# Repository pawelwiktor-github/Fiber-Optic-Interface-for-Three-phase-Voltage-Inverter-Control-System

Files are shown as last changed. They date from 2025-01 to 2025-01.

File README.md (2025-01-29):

# Fiber-Optic-Interface-for-Three-phase-Voltage-Inverter-Control-System

## Table of Contests

1. [Introduction](#introduction)
2. [Abstract of Thesis](#abstract-of-thesis)
3. [Usage Instructions](#usage-instructions)

## Introduction
This repository refers to the creation and implementation of the Fiber Optic Interface for Three phase Voltage Inverter Control System for PMSM motors. Every schematics, auxiliary files and performed steps are described in [engineering thesis](/thesis/Projekt%20i%20wykonanie%20interfejsu%20światłowodowego%20dla%20układu%20sterowania%20trójfazowego%20falownika%20napięcia%20dedykowanego%20dla%20silników%20PMSM.pdf). Main task was executed in Altium Designer Professional software ([engineering project](/main/Fibre-Optic-Interface.PrjPcb)). Additional documentations of used components and mechanical diagrams are stored in [doc](/doc/) folder.

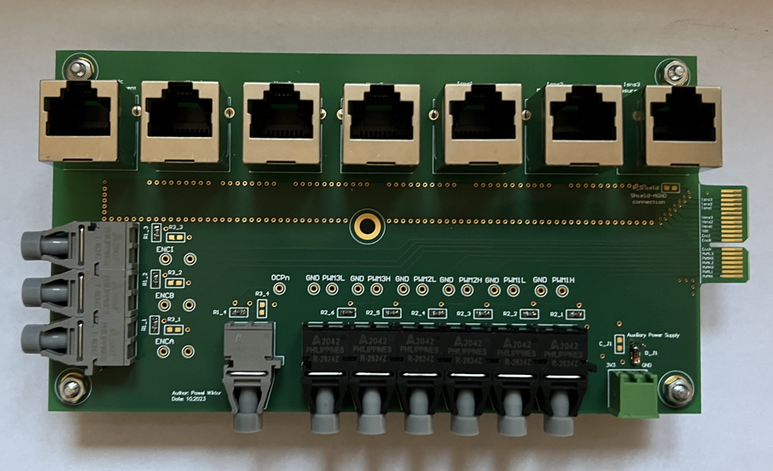
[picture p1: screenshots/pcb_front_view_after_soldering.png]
pcb_front_view
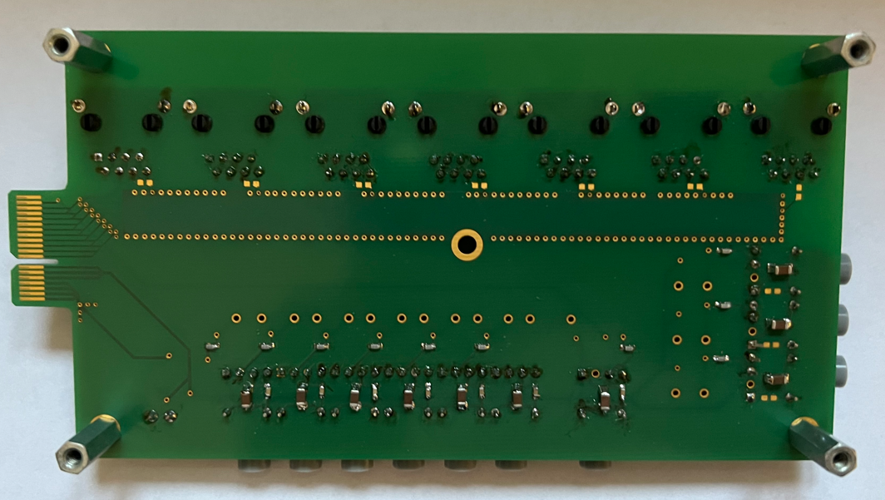
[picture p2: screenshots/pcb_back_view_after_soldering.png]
pcb_back_view
  

## Abstract of Thesis
The diploma project entitled as “Design and Implementation of Fiber Optic Interface for Three
phase Voltage Inverter Control System for PMSM Motors” describes steps related to the construction 
of a communication interface, which enables connection of three-phase voltage inverter module 
EPC9167 dedicated to drive systems with permanent magnet synchronous motors, made in “TTL” 
standard with a rapid prototyping controller B-BOX made in fiber-optic transmission standard.  
Engineering thesis includes a test bench description of the PMSM motor test system comprising 
of the above-mentioned components with their specifications, presents design requirements and 
created technical documentation of the interface and documents the assembly and testing processes.  
The project was finished with conclusions of communication interfaces designing process, an 
opinion on the encountered problems and opportunities for development. 

## Usage Instructions
**Prerequisites**:

***Software***:
   - Altium Designer Proffesional 24.8.2+

***Hardware***:
   - Fibre Optic Interface
   - BBox RCP Controller
   - PMSM Motor
   - EPC9167 (Three phase Voltage Inverter)

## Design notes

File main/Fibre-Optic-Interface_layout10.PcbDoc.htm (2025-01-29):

Reporting Options

# File in Newer Format

Date | : | 22.11.2023
Time | : | 11:46:45
Filename | : | C:\Users\Adam\Mój dysk (penczek@agh.edu.pl)\Dydaktyka\2023-24\Prace dyplomowe\Fibre_OPTIC\Altium\Fibre-Optic-Interface_rev9\Fibre-Optic-Interface\Fibre-Optic-Interface_layout10.PcbDoc

Version | Warning
Release 23.6 | CAUTION - The PCB document contains Footprint parameters. These will be lost when opening the document in a version of Altium Designer that does not support this functionality.

This file was generated by a later version of the software

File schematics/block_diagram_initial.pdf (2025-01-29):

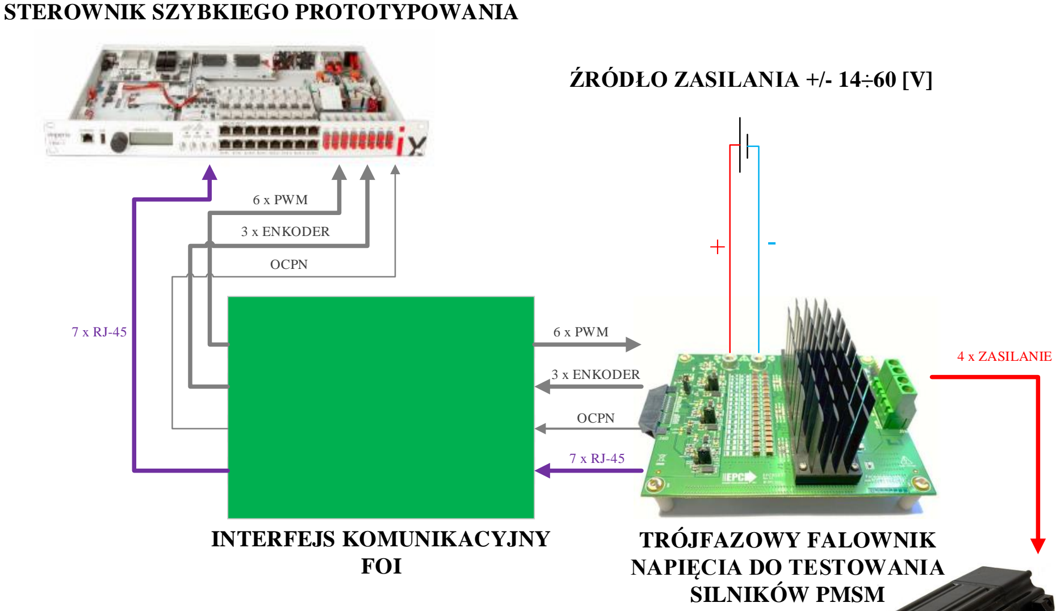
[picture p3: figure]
INTERFEJS KOMUNIKACYJNY FOI; STEROWNIK SZYBKIEGO PROTOTYPOWANIA; ŹRÓDŁO ZASILANIA +/- 14÷60 [V]; OCPN; 3 x ENKODER; 6 x PWM; TRÓJFAZOWY FALOWNIK; NAPIĘCIA DO TESTOWANIA SILNIKÓW PMSM; 4 x ZASILANIE
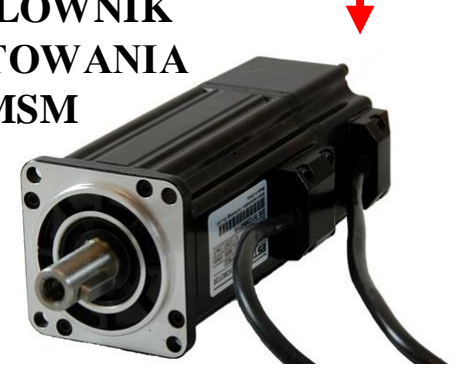
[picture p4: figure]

SILNIK PMSM

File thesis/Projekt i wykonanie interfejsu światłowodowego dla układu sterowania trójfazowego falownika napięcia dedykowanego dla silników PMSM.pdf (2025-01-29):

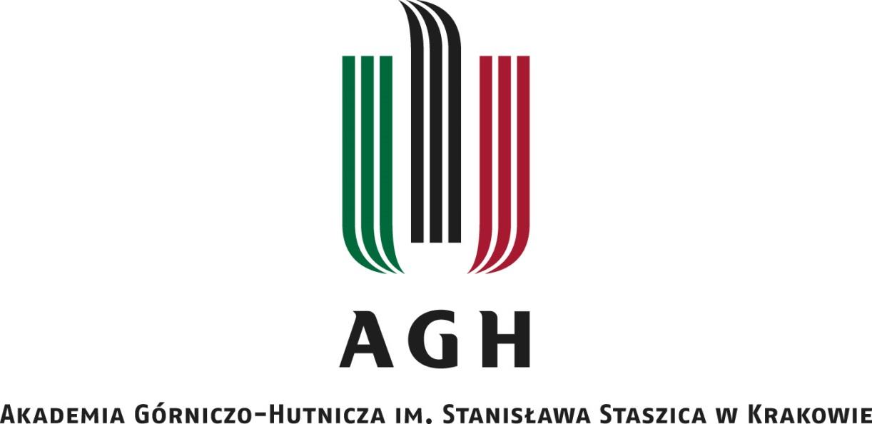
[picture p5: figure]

WYDZIAŁ ELEKTROTECHNIKI, AUTOMATYKI, INFORMATYKI I INŻYNIERII BIOMEDYCZNEJ

## Projekt dyplomowy

## Projekt i wykonanie interfejsu światłowodowego dla układu sterowania trójfazowego falownika napięcia dedykowanego dla silników PMSM Design and Implementation of Fiber Optic Interface for Three-phase Voltage Inverter Control System for PMSM Motors

Autor: | Paweł Wojciech Wiktor
Kierunek studiów: | Elektrotechnika
Opiekun pracy: | dr hab. inż. Adam Penczek

Kraków, 2024

Spis treści

Rozdział 3 – Projekt obwodu interfejsu światłowodowego dla układu sterowania trójfazowego

## Streszczenie

W projekcie dyplomowym pod tytułem „Projekt i wykonanie interfejsu światłowodowego dla układu sterowania trójfazowego falownika napięcia dedykowanego dla silników PMSM” opisano czynności związane ze skonstruowaniem interfejsu komunikacyjnego, który umożliwia połączenie wyprowadzeń obiektu w postaci modułu trójfazowego falownika napięcia EPC9167 dedykowanego
dla | układów | napędowych | z | silnikami | o | magnesach | trwałych, | wykonanych
w standardzie „TTL” wraz z wyprowadzeniami systemu szybkiego prototypowania dla układów sterowania B-BOX wykonanymi w standardzie transmisji światłowodowej.
W pracy inżynierskiej zawarto opis stanowiska badawczego systemu do testowania silników PMSM składającego się z wyżej wymienionych elementów wraz z ich specyfikacjami, przedstawiono założenia projektowe i stworzoną dokumentację techniczną interfejsu oraz udokumentowano procesy montażu i testowania.
Projekt zakończono podsumowaniem zawierającym wnioski dotyczące projektowania interfejsów komunikacyjnych, opinię na temat napotkanych problemów oraz możliwości rozwoju.

________________________________________________________________________________

## Abstract

The diploma project entitled as “Design and Implementation of Fiber Optic Interface for Three-phase Voltage Inverter Control System for PMSM Motors” describes steps related to the construction of a communication interface, which enables connection of three-phase voltage inverter module EPC9167 dedicated to drive systems with permanent magnet synchronous motors, made in “TTL” standard with a rapid prototyping controller B-BOX made in fiber-optic transmission standard. Engineering thesis includes a test bench description of the PMSM motor test system comprising of the above-mentioned components with their specifications, presents design requirements and created technical documentation of the interface and documents the assembly and testing processes. The project was finished with conclusions of communication interfaces designing process, an opinion on the encountered problems and opportunities for development.

## Rozdział 1. Wstęp

### 1.1. Wprowadzenie

Rozwój technologii w dziedzinie elektroniki mocy oraz sterowania silnikami stawia przed projektantami wyzwania związane z minimalizacją rozmiaru, zwiększaniem funkcjonalności i sprawności oraz ze zmniejszaniem poboru energii. Jednym z rozwiązań jest implementacja zaawansowanych układów elektronicznych zmieniających napięcie stałe na napięcie zmienne w procesie sterowania silnikami PMSM.
Silniki PMSM zyskują coraz większą popularność jako urządzenia wykorzystane na przykład w sprzętach AGD domowego użytku ze względu na swoje właściwości dynamiczne, wysoką sprawność oraz niskie zużycie energii.
Przed przystąpieniem do masowej produkcji konkretnego systemu należy określić zapotrzebowanie ilości sygnałów sterujących i parametrów sterowania. W fazie testowania można do tego wykorzystać sterowniki szybkiego prototypowania, które posiadają „przewymiarowaną” oraz zróżnicowaną ilość wyprowadzeń zarówno cyfrowych jak i analogowych.
Wśród sterowników szybkiego prototypowania, korzystnym wyborem są modele oparte na technologii w standardzie transmisji światłowodowej. Zaletami takiego rozwiązania jest możliwość propagacji danych na duże odległości, eliminacja problemów związanych z utratą sygnału, niski czas propagacji czy brak utraty jakości sygnału.
Aby była możliwość implementacji systemu szybkiego prototypowania, należy dopasować standard wyprowadzeń tego systemu do obiektu sterowanego. Zapewnienie komunikacji pomiędzy urządzeniami, które mają skonfigurowane wejścia i wyjścia w różnych standardach można uzyskać poprzez stworzenie interfejsu komunikacyjnego.
W przypadku standardu transmisji światłowodowej, wykorzystuje się interfejsy oparte na konwerterach, które oprócz translacji światłowodowo-elektrycznej zapewniają izolację galwaniczną – jeden z wymogów układów prototypowania.

### 1.2. Cel oraz zakres projektu dyplomowego

Celem projektu dyplomowego jest stworzenie obwodu drukowanego, umożliwiającego połączenie obiektu w postaci trójfazowego falownika napięcia EPC9167 dedykowanego do obsługi układów napędowych z silnikami PMSM z systemem szybkiego prototypowania układów sterowania B-BOX firmy „imperix”.
Podstawową funkcją jaką ma spełniać projektowany układ jest konwersja sygnałów logicznych w standardzie transmisji światłowodowej obsługiwanych przez sterownik B-BOX na cyfrowe sygnały elektryczne w standardzie „TTL” obsługiwane przez moduł falownika. Dodatkową funkcją jest rozprowadzenie sygnałów pomiarowych w standardzie analogowym wykorzystując złącza RJ-45 tak, aby można je było w łatwy sposób podłączyć do sterownika B-BOX.
Projekt dyplomowy obejmuje swym zakresem podział na trzy etapy.

W pierwszej części należy wykonać opis systemu, dla którego projektowany jest interfejs, czyli układu do szybkiego prototypowania systemów sterowania dla zespołów napędowych takich jak silniki PMSM, który zawiera obiekt sterowany w postaci silnika i modułu trójfazowego falownika napięcia oraz obiekt wymuszający w postaci sterownika RCP.
W etapie drugim nazwanym jako etap projektowy należy przedstawić założenia projektowe oraz zaprezentować stworzoną dokumentację techniczną interfejsu światłowodowego. Do stworzenia dokumentacji przewidziano wykorzystanie profesjonalnego oprogramowania „Altium Designer Professional (23.9.2)”.
Po uzyskaniu egzemplarza płytki, w ostatnim etapie należy zawrzeć opis procesu montażu oraz procesów testowania układu.

## Rozdział 2 – Opis systemu sterowania dla silników PMSM

Celem projektu było skonstruowanie urządzenia umożliwiającego połączenie sterownika B-BOX firmy „imperix”, którego wyprowadzenia wykonano w standardzie transmisji światłowodowej oraz modułu trójfazowego falownika EPC9167 firmy „EPC” o wyprowadzeniach wykonanych w standardzie „TTL”. Obiekt sterowany w postaci silnika z przekształtnikiem DC/AC, obiekt wymuszający w postaci systemu szybkiego prototypowania układów sterowania oraz interfejs komunikacyjny tworzą stanowisko do testowania układów napędowych pokroju silników PMSM, którego schemat blokowy zaprezentowano na rysunku 1.

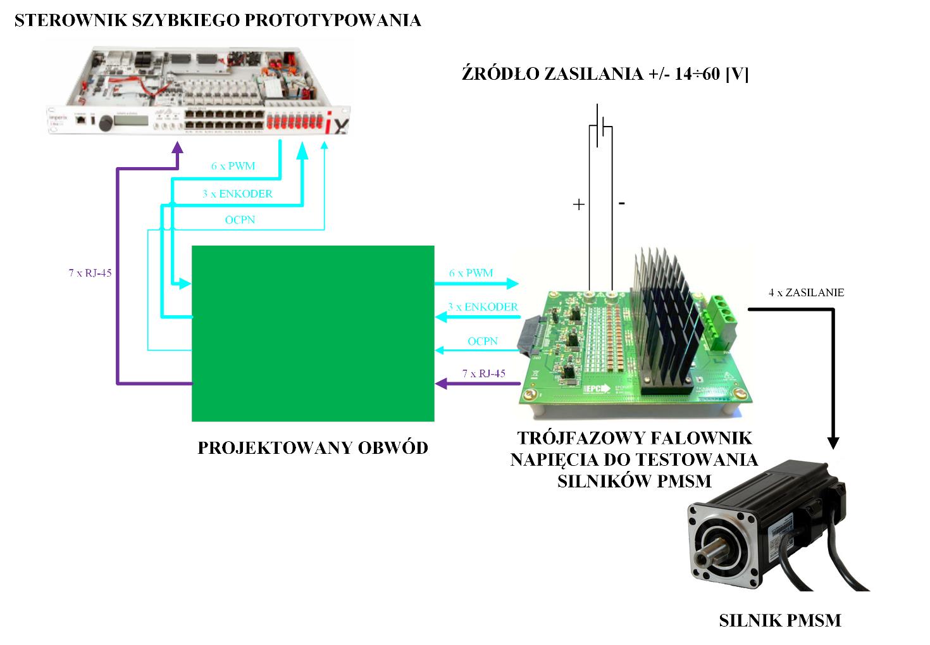
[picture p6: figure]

Rysunek 1. Schemat blokowy systemu sterowania

### 2.1. Sterownik B-BOX RCP

Sterownik B-BOX firmy „imperix” to system szybkiego prototypowania układów sterowania. Do zalet tego modelu zalicza się możliwość testowania układów obciążenia z racji posiadania większej ilości wejść i wyjść niż wymaga tego aplikacja oraz możliwość programowania blokowego, które jest proste oraz wygodne w obsłudze dla użytkownika. Na rysunku 2 przedstawiono zdjęcie sterownika B-BOX RCP.

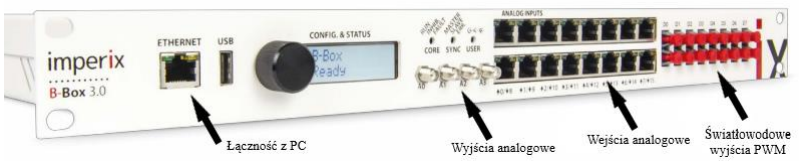
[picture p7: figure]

Rysunek 2. Zdjęcie sterownika imperix B-BOX RCP [1]

Model wyróżnia się zaawansowanymi możliwościami modulacji szerokości impulsu oraz licznymi wejściami/wyjściami analogowymi i cyfrowymi. Posiada również możliwość łączności z komputerem, a więc umożliwia współpracę ze zintegrowanym środowiskiem projektowania algorytmów blokowych pokroju oprogramowania „Matlab” z rozszerzeniem „Simulink”. Sterownik posiada wyprowadzenia wejść analogowych w standardzie RJ-45. Koncepcję przyłączenia sygnałów do pinów złącza przewidywaną przez producenta przedstawiono na rysunku 3.

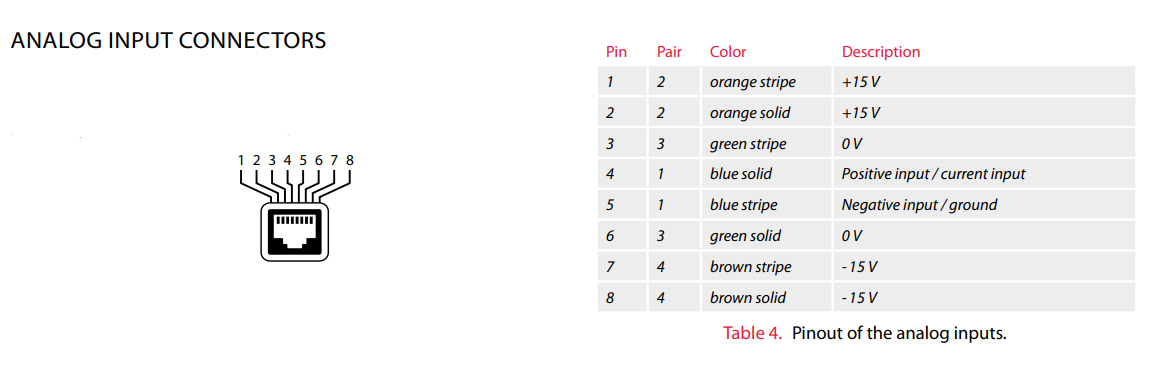
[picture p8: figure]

Rysunek 3. Koncepcja przyłączenia sygnałów do pinów złącza RJ-45 [1]

W tabeli 1 wyszczególniono główne specyfikacje sterownika, które są wykorzystywane przez aplikację FOI.

Tabela 1. Specyfikacje sterownika "B-BOX RCP" [1]

Komponent | Specyfikacja
Chip systemowy | Xilinx Zynq XC7030-3FBG676E, Klasa prędkości -3
System przetwarzania | ARM Cortex A9 1 [GHz] (2szt.), 1 [GB] DDR3
Programowalny układ logiczny (FPGA) | Kintex7 125K, Artix 7 35T (pomocniczy)
Przechowywanie | Pamięć flash 16 [MB] (2szt.), micro SD + eMMC 8 [GB]
Wyjścia PWM | Różne modulatory, rozdzielczość 4 [ns]
Optyczne 50 [Mb/s] (16szt.) Elektryczne [3.3 V] (32szt.)
Wejścia analogowe | 16 bitów / 500 ksps jednocześnie (16szt.) + w pełni konfigurowalny front-end
Szybkie wejścia/wyjścia użytkownika | FPGA bezpośrednie [3.3 V] (36szt.)
Wejścia/wyjścia błędów | Cyfrowe [3.3 V] (16szt.), blokada optyczna, blokada elektryczna [5 V]

Szczegółowa specyfikacja oraz schematy poszczególnych komponentów znajdują się w dokumentacji technicznej sterownika umieszczonej jako załącznik 1 niniejszej pracy.

### 2.2. Moduł trójfazowego falownika napięcia

EPC9167 to zestaw uruchomieniowy trójfazowego falownika napięcia dedykowany dla silników PMSM. Działanie modułu falownika opiera się na wykorzystaniu dwunastu tranzystorów FET typu „EPC2065 eGaN”, gdzie para równoległych połączeń dwóch tranzystorów (w sumie czterech sztuk) w topologii mostkowej przypada na jedną fazę obwodu. Na rysunku 4 umieszczono schemat elektryczny modułu trójfazowego falownika napięcia.

Rysunek 4. Schemat elektryczny modułu trójfazowego falownika napięcia [2]

Podstawowa konfiguracja zakłada sterowanie silnikiem o magnesach trwałych. Układ zawiera element łączeniowy z interfejsem komunikacyjnym oraz z obiektem obciążenia. Oprócz aplikacji tranzystorów, układ zawiera element wykrywający wystąpienie przeciążenia prądowego, wzmacniacze operacyjne czy wyprowadzenia pod czujniki takie jak enkoder czy czujnik Halla. Rysunek 5 przedstawia zdjęcie modułu trójfazowego falownika napięcia.

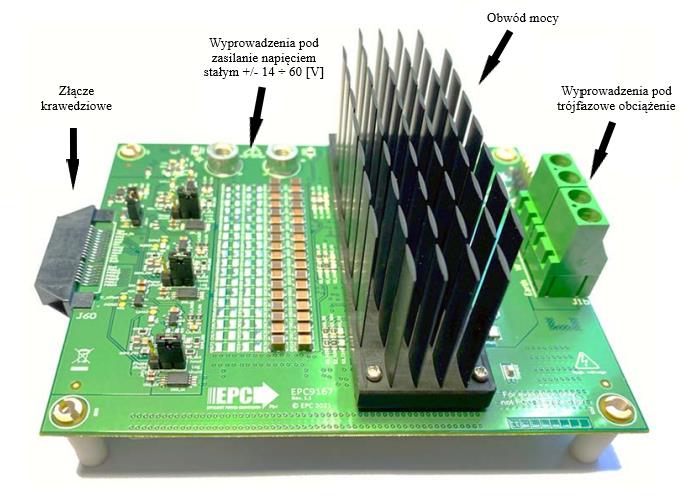
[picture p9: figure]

Rysunek 5. Zdjęcie modułu trójfazowego falownika napięcia [2]

Na złączu krawędziowym oznaczonym przez producenta jako J60 zostały wyprowadzone sygnały analogowe pozyskane z czujników prądów i napięć, sygnały cyfrowe, czyli wejścia sterujące, wyjścia z enkodera oraz sygnały błędów. Moduł falownika posiada wyprowadzenia pod zewnętrzne zasilanie napięciem stałym. Z dokumentacji technicznej wynika, że nominalne napięcie zasilania to 48 [V], natomiast jest możliwość podpięcia napięcia zasilającego na zakresie (±14÷60 [V]). Na rysunku 5 oznaczono również obwód mocy, którym jest trójfazowy falownik napięcia wraz z układem chłodzenia oraz czterobiegunowe złącze przeznaczone do podłączenia trójfazowego układu obciążenia, domyślnie przewidzianego jako silnik PMSM.

Moduł falownika wyposażony jest między innymi w sterowniki bramkowe i wbudowany zasilacz podtrzymujący logikę, czujniki prądu i napięcia dla wszystkich faz oraz czujnik napięcia stałego, czujnik temperatury „U40-AD590” czy wskaźniki LED.

Płytka posiada układ zabezpieczenia nadprądowego, które jest uruchamiane, jeśli wartość chwilowa prądu na jednej z faz przekroczy 50 [A]. Istnieje możliwość konfiguracji układu do detekcji przeciążenia prądowego, która przez złącze krawędziowe jest w stanie wysyłać sygnał do użytkownika, informujący o wystąpieniu przeciążenia. [2]

Szczegółowe specyfikacje znajdują się w dokumentacji techniczno-ruchowej umieszczonej jako załącznik 2 niniejszej pracy.

### 2.3. Silnik PMSM

Silnik PMSM (ang. Permament Magnet Synchrous Motor) to rodzaj synchronicznego silnika elektrycznego o magnesach trwałych na uzwojeniu wirnika oraz stojana. Jest to urządzenie, które osiąga stan równowagi podczas synchronizacji pracy obracania się wirnika z częstotliwością zasilającego prądu. Wśród kategorii silników synchronicznych wyróżnia się tym, że proces przekazywania wartości kąta obrotu wirnika odbywa się w sposób ciągły oraz praca uwzględnia sprzężenie zwrotne.
Wykorzystywany jest najczęściej w domowych sprzętach AGD lub w elektrycznym przemyśle transportu ze względu na wysoką sprawność, brak konieczności dostarczania energii do magnesów czy możliwości precyzyjnego ustalania pozycji oraz prędkości.
Silnik PMSM zasilany jest napięciem przemiennym oraz można go zdefiniować jako urządzenie o sinusoidalnych prądach oraz sinusoidalnym kształcie sił elektromotorycznych. [3]

## Rozdział 3 – Projekt obwodu interfejsu światłowodowego dla

## układu sterowania trójfazowego falownika napięcia

Głównym zadaniem interfejsu światłowodowego w systemie do testowania silników PMSM była dwukierunkowa konwersja elektryczno-światłowodowa. Dodatkowo interfejs miał umożliwić propagację pomiarowych sygnałów w standardzie analogowym. Na rysunku 6 przedstawiono schemat ideowy systemu sterowania.

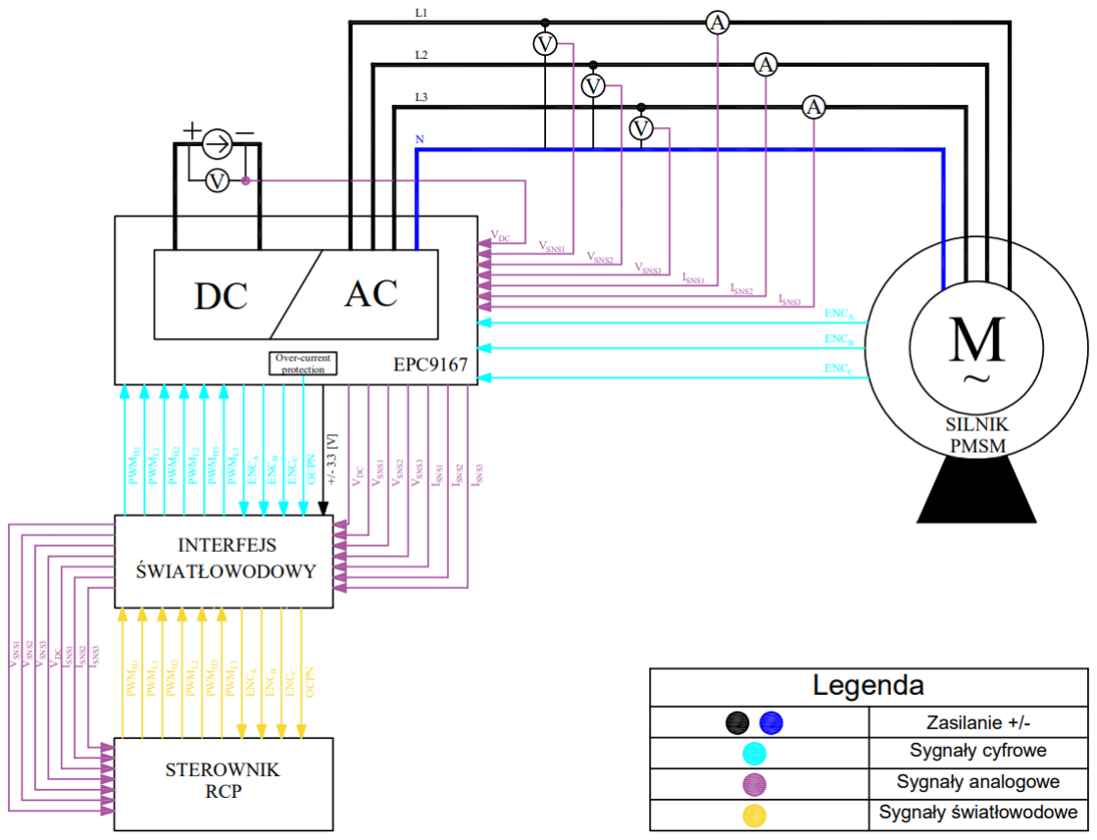
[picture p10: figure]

Rysunek 6. Schemat ideowy systemu sterowania

Opis indeksowania sygnałów cyfrowych oraz analogowych umieszczono w tabeli 2.

Tabela 2. Opis indeksowania sygnałów cyfrowych oraz analogowych

Indeks | Opis
PWMH1, PWMH2, PWMH3, PWML1, PWML2, PWML3 | Sygnały modulacji szerokości impulsu
ENCA, ENCB, ENCC | Sygnały z enkodera
OCPN | Sygnał zabezpieczenia nadprądowego
VDC | Sygnał pomiaru napięcia stałego
VSNS1, VSNS2, VSNS3 | Sygnały pomiaru zmiennych napięć fazowych
ISNS1, ISNS2, ISNS3 | Sygnały pomiaru zmiennych prądów fazowych

### 3.1. Założenia projektowe

Stworzenie dokumentacji technicznej interfejsu przewidziano w oprogramowaniu „Altium Designer”. Jest to specjalistyczna aplikacja umożliwiająca tworzenie obwodów drukowanych od koncepcji projektowej do przygotowania plików potrzebnych do realizacji produkcyjnej.

W założeniach projektowych określono wymagania zarówno mechaniczne jak i elektryczne. Oprogramowanie „Altium Designer” umożliwia użytkownikowi definicję ustawień projektowych określających szerokości ścieżek, odstępy pomiędzy elementami, rozmiary przelotek czy definicję obwodu o wspólnej masie. Ustawienie zasad projektowych umożliwia w przyszłości unikanie błędów oraz wygodne sprawdzanie poprawności wykorzystując opcję dostępne w programie. [4] Założenia projektowe przedstawiono w tabeli 3.

Tabela 3. Założenia projektowe

Założenia projektowe

1. Wykonanie obwodu drukowanego o wymiarach nie większych niż 260x100 [mm] (długość x szerokość)
2. Zaprojektowanie sześciu konwerterów światłowodowo-elektrycznych (odbiorniki)
3. Zaprojektowanie czterech konwerterów elektryczno-światłowodowych (nadajniki)
4. Zaprojektowanie siedmiu złącz RJ-45 umożliwiających propagację analogowych sygnałów pomiarowych
5. Doprowadzenie zasilania do układu o wartości ± 3,3 [V]
6. Założenia dotyczące wymagań elektrycznych podczas projektowania płytki:
- Wartość odstępów elektrycznych dla elementów na poziomie 10 [mils]
- Szerokość ścieżek sygnałów cyfrowych i analogowych w zakresie (10 ÷ 20) [mils]
- Szerokość ścieżek sygnałów zasilających i uziemiających w zakresie (15 ÷ 30) [mils]
- Wymiary przelotek dla części analogowej: średnica przejścia w zakresie (20 ÷ 40) [mils] oraz średnica otworu w zakresie (10 ÷ 20) [mils]
- Wymiary przelotek dla części cyfrowej i zasilającej: średnica przejścia w zakresie (30 ÷ 60) [mils] oraz średnica otworu w zakresie (10 ÷ 30) [mils]

Założono, że wymiary interfejsu światłowodowego FOI nie powinny przekroczyć dwukrotności długości, czyli 260 [mm] oraz szerokości, czyli 100 [mm] płytki EPC9167. Założenia dotyczące wymagań elektrycznych odnoszą się do możliwości technologicznych. Wartości dobrano możliwie najniższe jednocześnie zachowując wymagania pochodzące z norm, pozwalające uniknąć uszkodzeń mechanicznych.

### 3.2. Koncepcja rozmieszczenia elementów na płytce PCB

Mając na uwadze nadrzędne funkcje interfejsu komunikacyjnego takie jak dwukierunkowa konwersja elektryczno-światłowodowa oraz propagacja pomiarowych sygnałów w standardzie analogowym zdecydowano się na podział planowania obwodu na cztery sekcje: sekcję złącza sygnałowego, sekcję translacji światłowodowo-elektrycznej, sekcję translacji elektryczno-światłowodowej oraz sekcję złącz pomiarowych. Na rysunku 7 umieszczono koncepcję rozmieszczenia elementów na płytce FOI.

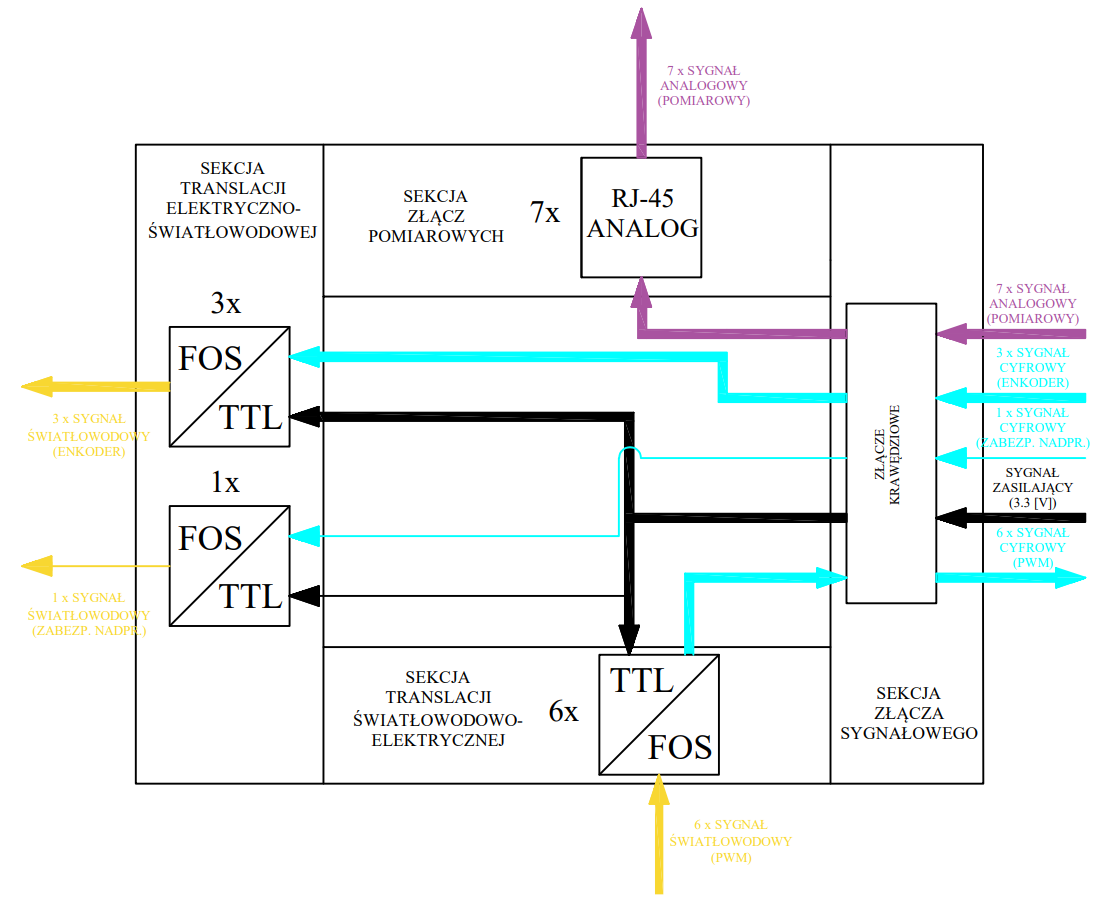
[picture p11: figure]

Rysunek 7. Koncepcja rozmieszczenia elementów na płytce FOI

Złącze krawędziowe przewidziane w sekcji złącza sygnałowego to fizyczny element łączeniowy modułu falownika oraz FOI. Odpowiada za przekazanie sygnałów zasilających na poziomie napięcia wynoszącym ± 3,3 [V], sygnałów uziemiających, sygnałów pomiarowych oraz sterujących.
W sekcji translacji światłowodowo-elektrycznej przewidziano sześć konwerterów o indeksie „TTL/FOS”. „TTL” (ang. Transistor-Transistor Logic) to technologia logicznych sygnałów cyfrowych w standardzie maksymalnie pięciowoltowym, natomiast „FOS” (ang. Fibre Optic Signal) to technologia sygnałów w standardzie transmisji światłowodowej.
W sekcji translacji elektryczno-światłowodowej zaplanowano umieszczenie trzech nadajników oznaczonych koncepcyjnie jako „FOS/TTL”, których zadaniem była konwersja sygnałów pochodzących z enkodera oraz nadajnika obsługującego sygnał wyzwolenia układu zabezpieczenia nadprądowego.
W sekcji złącz pomiarowych przewidziano siedem złącz RJ-45, które umożliwiają przekazanie sygnałów pomiaru napięcia stałego, pomiaru napięć fazowych oraz pomiaru prądów fazowych do sterownika B-BOX.

### 3.3. Schemat elektryczny

Na rysunku 8 zaprezentowano schemat elektryczny projektowanego obwodu PCB. Na schemacie można wyróżnić następujące sekcje:

- Sekcja złącza sygnałowego (na schemacie oznaczona kolorem czerwonym)
- Sekcja wejść/wyjść cyfrowych (na schemacie oznaczona kolorem zielonym)
- Sekcja wyjść analogowych (na schemacie oznaczona kolorem fioletowym)

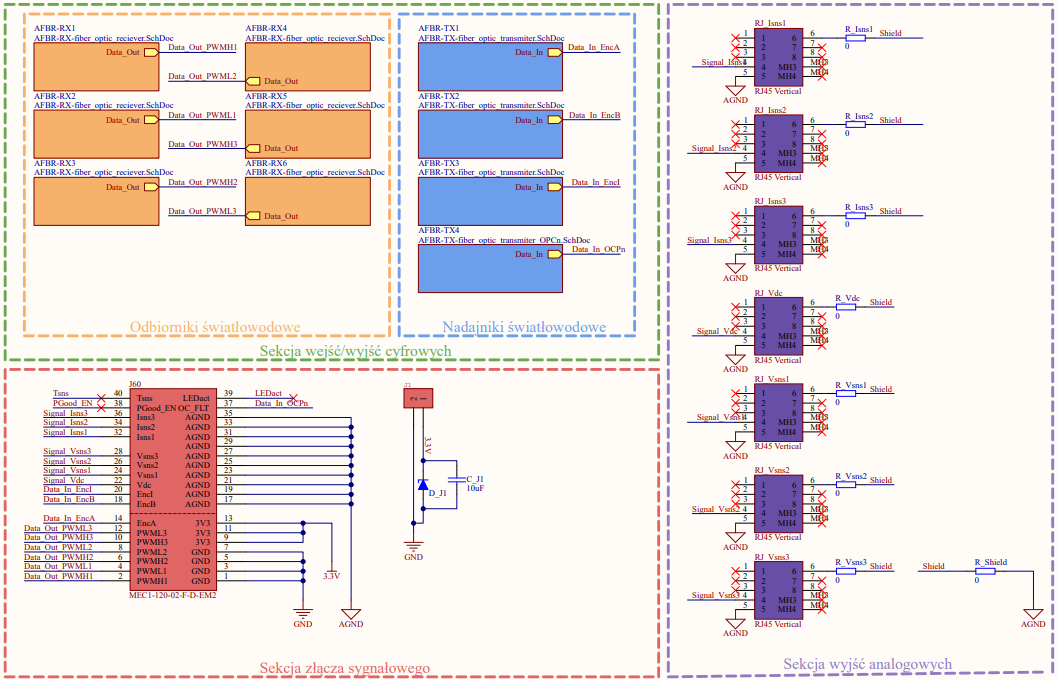
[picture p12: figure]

Rysunek 8. Schemat główny

3.3.1. Sekcja złącza sygnałowego

W sekcji złącza sygnałowego umieszczono blok złącza krawędziowego, którego fizyczna wersja znajduje się na płytce EPC9167 oraz blok dodatkowego złącza zasilającego. Rysunek 9 przedstawia część schematu głównego ilustrującą sekcje złącza sygnałowego.

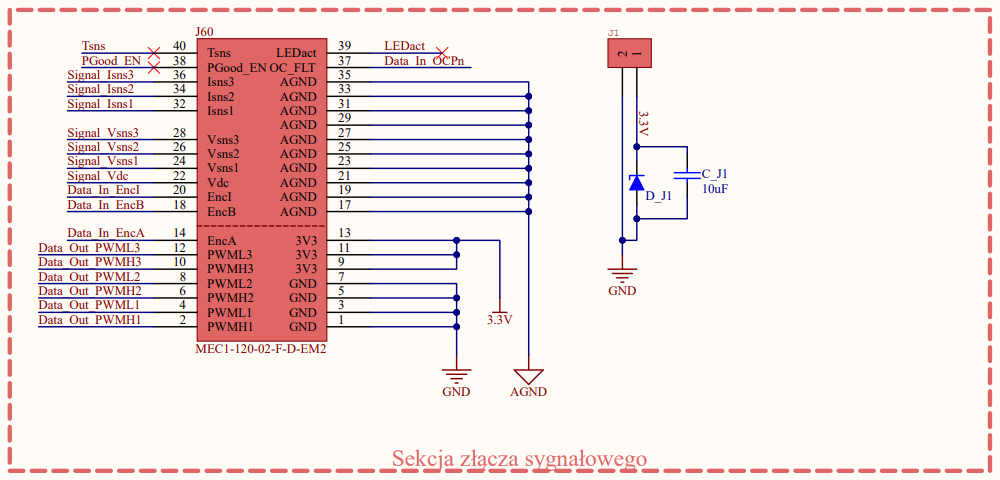
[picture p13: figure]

Rysunek 9. Schemat elektryczny sekcji złącza sygnałowego

3.3.1.1. Złącze krawędziowe J60, model MEC1-120-02-F-D-EM2

Złącze krawędziowe MEC1-120-02-F-D-EM2 firmy „Samtec” to czterdziesto-pinowe element, który został przewidziany przez producenta EPC9167 do przesyłania sygnałów sterujących, pomiarowych oraz zasilających do interfejsu komunikacyjnego (Rysunek 10).

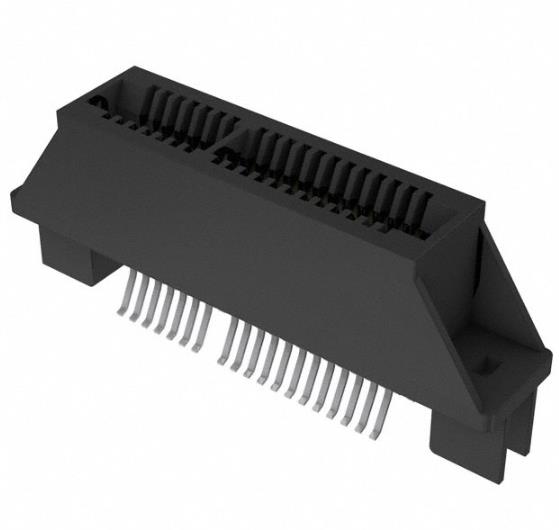
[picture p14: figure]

Rysunek 10. Zdjęcie złącza krawędziowego, model MEC1-120-02-F-D-EM2 [5]

Spośród dostępnych rozwiązań, zdecydowano się na wymiarowe dopasowanie krawędzi obwodu FOI oraz wyprowadzenie ścieżek co w założeniu miało umożliwić nałożenie płytek na siebie w celu uzyskania komunikacji. Na rysunku 11 umieszczono fragment dokumentacji złącza, która stanowi załącznik 3 niniejszej pracy.

Rysunek 11. Fragment dokumentacji technicznej złącza MEC1-120-02-F-D-EM2 [6]

Na podstawie danych z dokumentacji mechanicznej udostępnionej przez producenta takich jak szerokość pojedynczego wyprowadzenia, odległości pomiędzy wyprowadzeniami, wymiary wcięć oraz kształt i wymiary krawędzi złącza zaprojektowano wcześniej wspomniane połączenie.

3.3.1.2. Złącze J1

Złącze J1 posiada dwa wyprowadzenia nadające się do doprowadzenia zewnętrznego zasilania. Umieszczono je podczas projektowania obwodu w celu dostarczenia sygnału zasilającego w fazie testowania przed podłączeniem do modułu falownika.

3.3.2. Sekcja wejść/wyjść cyfrowych

W sekcji wejść/wyjść cyfrowych, której schemat przedstawiono na rysunku 12 umieszczono konwertery światłowodowe (odbiorniki i nadajniki),

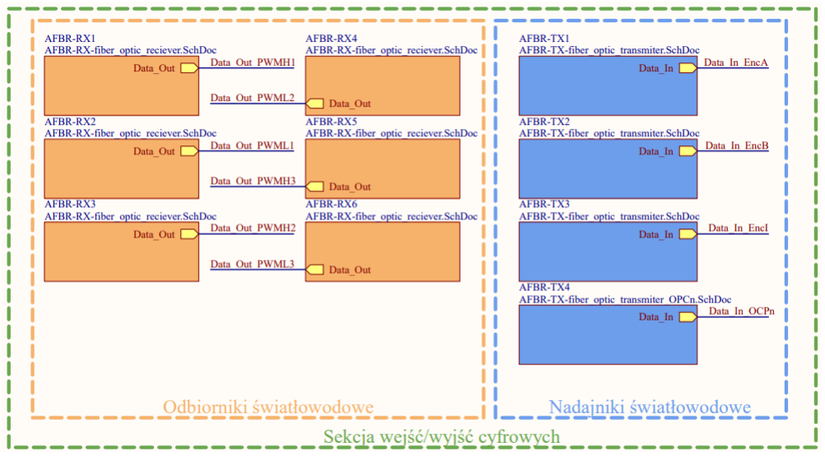
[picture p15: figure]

Rysunek 12. Schemat elektryczny sekcji wejść/wyjść cyfrowych

Bloki odbiorników oznaczone na schemacie kolorem pomarańczowym posiadają port wyjściowy w postaci wyprowadzenia przekonwertowanego sygnału modulacji szerokości impulsu, natomiast bloki nadajników oznaczone na schemacie kolorem niebieskim posiadają port wejściowy w postaci wyprowadzenia sygnałów pochodzących z enkodera oraz z obwodu wykrywającego wystąpienie przeciążenia prądowego w standardzie „TTL”.

3.3.2.1. Odbiornik światłowodowy, model AFBR-2624Z

Konwerter firmy „Broadcom” służący do translacji światłowodowo-elektrycznej został wykonany w wersji pionowej ze względu na umiejscowienie przyłącza pod przewód światłowodowy. Na rysunkach 13 oraz 14 umieszczono zdjęcie odbiornika światłowodowego oraz zaprojektowany schemat elektryczny pojedynczego kanału na podstawie noty aplikacyjnej od producenta.

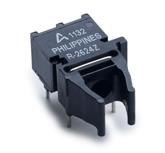
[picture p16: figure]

Rysunek 13. Odbiornik światłowodowy, model AFBR-2624Z [7]

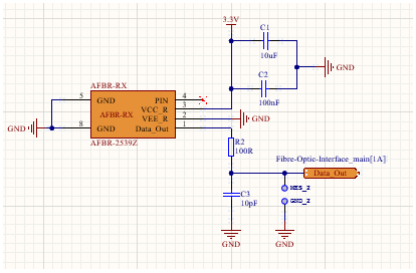
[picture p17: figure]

Rysunek 14. Schemat elektryczny odbiornika światłowodowego

Na linii sygnałowej przyłączonej do wyprowadzenia „Data_Out” umieszczono filtr dolnoprzepustowy RC w celu blokowania częstotliwości o wartościach wyższych niż wartość częstotliwości odcięcia oraz punkty umożliwiające podłączenie sondy pomiarowej wyposażonej w elektrody przeciwnych biegunów, pozwalającej zweryfikować poprawność zaprojektowania ścieżek czy ilustracji przebiegu na ekranie oscyloskopu.

Na wyprowadzenie „VCC_R” dostarczano zasilanie do urządzenia. Na linii zasilającej umieszczono dwa kondensatory stabilizujące napięcie. Umieszczenie ich możliwie jak najbliżej konwerterów pozwala na minimalizacje zakłóceń za pośrednictwem skrócenia ścieżki prądowej.

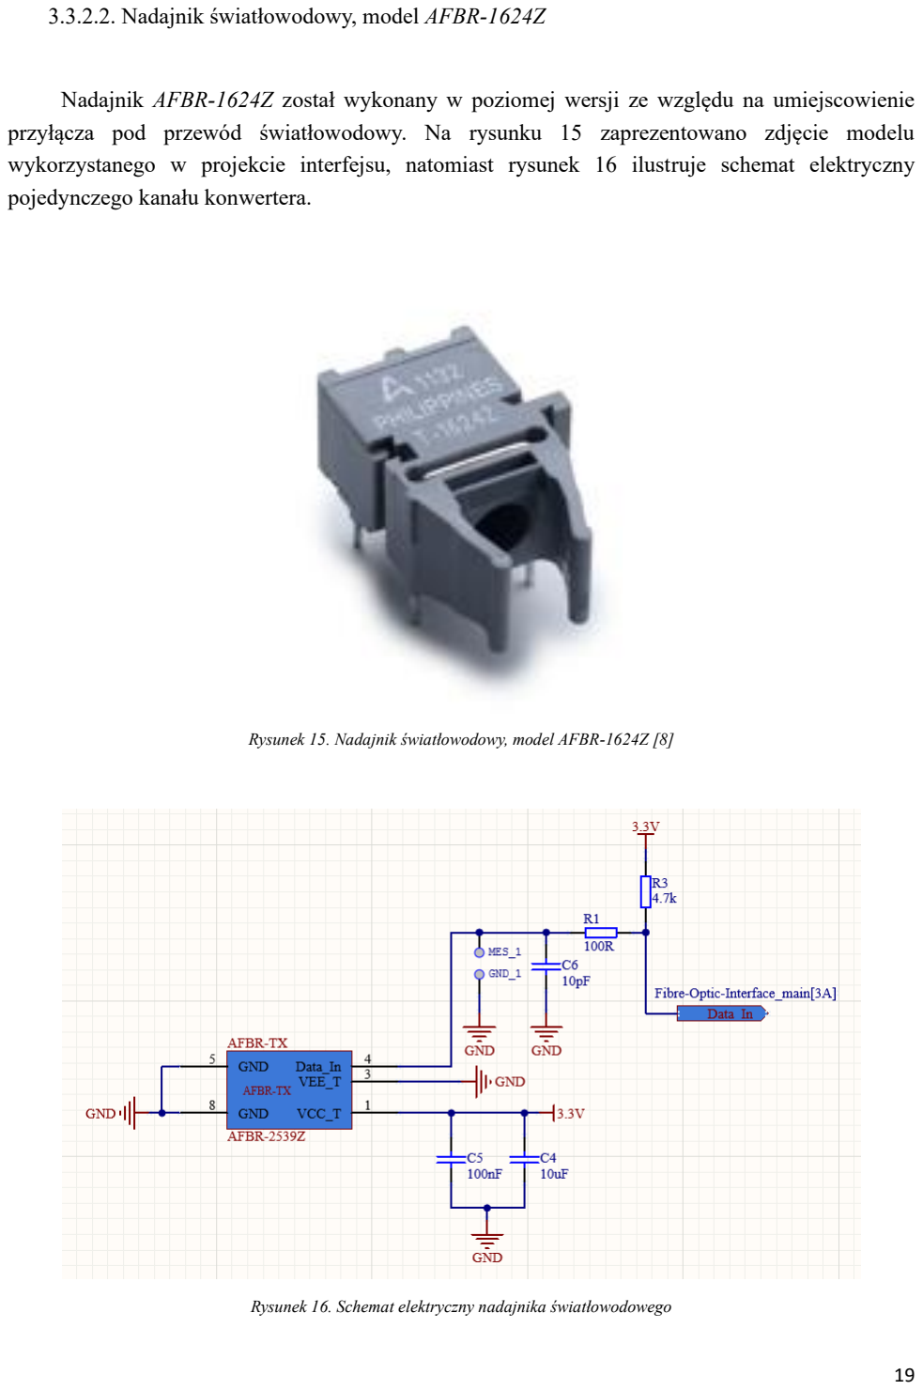
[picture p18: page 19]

3.3.2.2. Nadajnik światłowodowy, model AFBR-1624Z

Nadajnik AFBR-1624Z został wykonany w poziomej wersji ze względu na umiejscowienie przyłącza pod przewód światłowodowy. Na rysunku 15 zaprezentowano zdjęcie modelu wykorzystanego w projekcie interfejsu, natomiast rysunek 16 ilustruje schemat elektryczny pojedynczego kanału konwertera.

Rysunek 15. Nadajnik światłowodowy, model AFBR-1624Z [8]

Rysunek 16. Schemat elektryczny nadajnika światłowodowego

W aplikacji nadajnika również umieszczono kondensatory stabilizujące napięcie oraz filtr RC. Zgodnie z zaleceniami producenta, na linii zasilającej w celu zapewnienia stabilizacji napięcia oprócz kondensatorów dodatkowo umieszczono rezystor typu „pull-up”

W konwerterach odpowiedzialnych za sygnały pochodzące z enkodera zastosowano dwa punkty pomiarowe, natomiast w konwerterze obsługującym sygnał błędu nadprądowego zastosowano jeden punkt o indeksie „OCPn”.

3.3.3. Sekcja wyjść analogowych

W sekcji wyjść analogowych, której schemat elektryczny umieszczono na rysunku 17 przewidziano umieszczenie siedmiu złącz RJ-45.

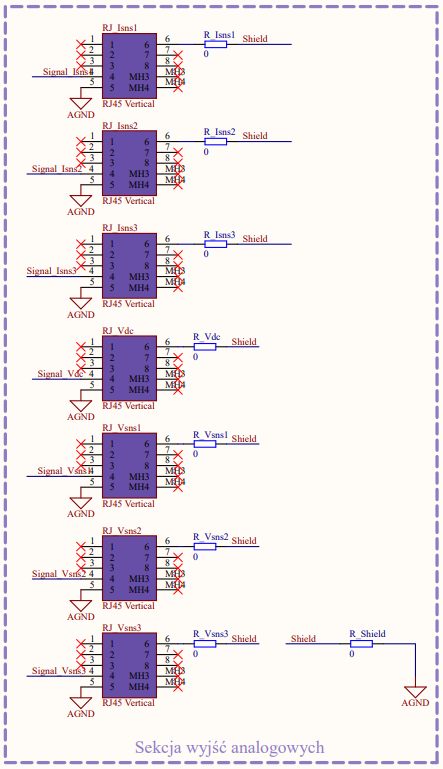
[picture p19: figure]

Rysunek 17. Schemat elektryczny sekcji wyjść analogowych

3.3.3.1. Złącze pomiarowe typu RJ-45, model CUC-SP-J1ST-S/R4LT

W projekcie wykorzystano model CUC-SP-J1ST-S/R4LT firmy „Phoenix Contact”, którego zdjęcie zaprezentowano na rysunku 18.

Rysunek 18. Zdjęcie złącza typu RJ-45, model CUC-SP-J1ST-S/R4LT [9]

Model CUC-SP-J1ST-S/R4LT to standardowe, ośmio-pinowe złącze typu RJ-45 wykonane w standardzie ethernetowym o przewlekanym rodzaju montażu.

W odwołaniu do rysunku 3 przedstawiającego opis przeznaczenia pinów, na potrzeby tytułowego interfejsu wykorzystano wyprowadzenia odpowiedzialne za sygnał prądowy oraz sygnał uziemiający. Szóste wyprowadzenie o zerowym potencjale przewidziano na połączenie z ekranem analogowym wykorzystując rezystor o maksymalnie niskiej rezystancji.

### 3.4. – Wykonanie obwodu

Stosując się do założeń projektowych oraz zgodnie z koncepcją umieszczoną na rysunku 7 rozmieszczono elementy na płytce PCB.

3.4.1. Widok ogólny

Ogólna wizualizacja dwuwymiarowa to przekrojowy widok warstw sygnałowych płytki patrząc z góry. Na rysunku 19 zaprezentowano widok ogólny płytki FOI.

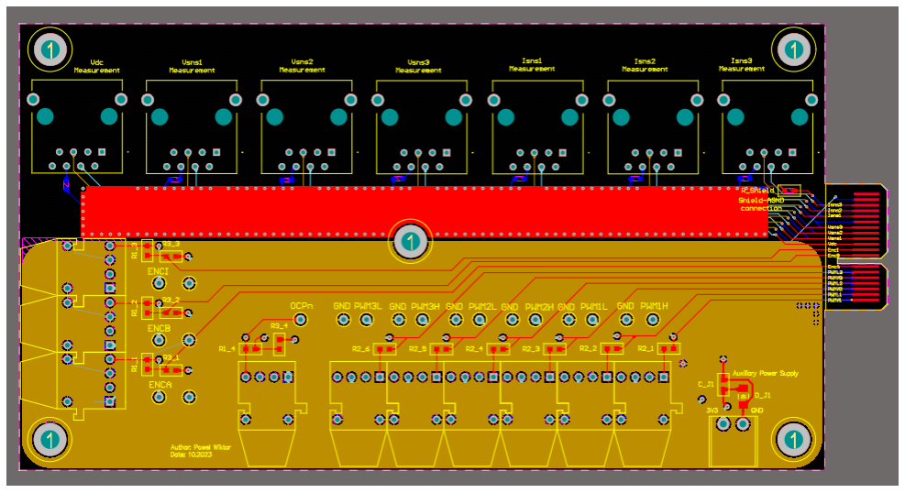
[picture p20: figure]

Rysunek 19. Widok ogólny płytki FOI

Płytkę FOI zaprojektowano jako czterowarstwowy obwód drukowany o wymiarach 155 x 80 [mm]. W celu zabezpieczenia przed uszkodzeniami mechanicznymi umieszczono podpory w postaci pięciu śrub M3.

Zdecydowano się na umieszczenie ekranu izolującego w celu separacji sygnałów analogowych od sygnałów cyfrowych. Separacja z wykorzystaniem ekranu pozwala na minimalizacje zakłóceń elektromagnetycznych.

W prawej części widoku umieszczono wycięty fragment obwodu odpowiadający za połączenie z konektorem J60 zgodnie z dokumentacją techniczną złącza MEC1-120-02-F-D-EM2.

3.4.2. Widok zewnętrznej warstwy górnej – Top Layer

Projekt zakłada dwie warstwy zewnętrzne umożliwiające rozmieszczanie elementów. Jedną z nich jest warstwa górna, której wizualizację dwuwymiarową przedstawiono na rysunku 20.

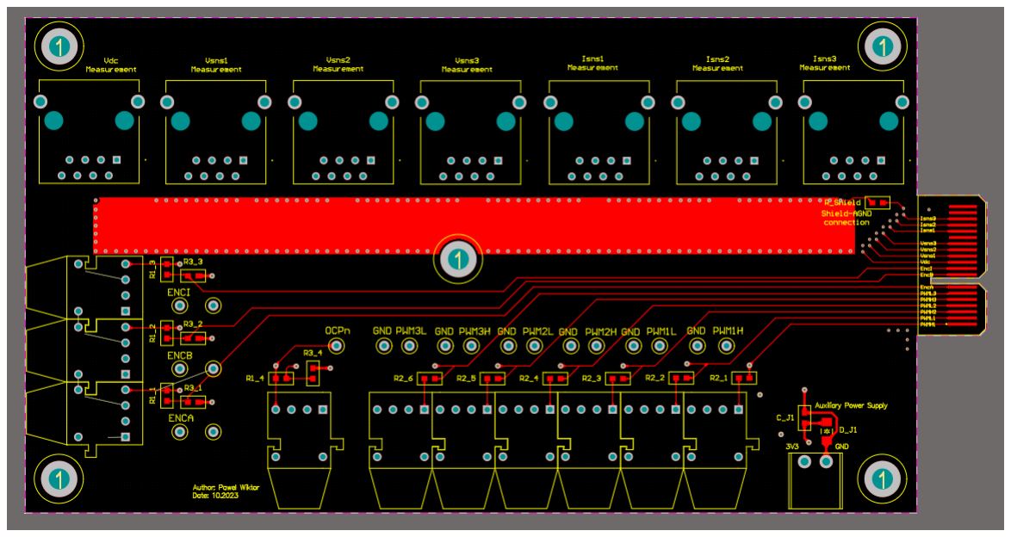
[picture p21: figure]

Rysunek 20. Widok zewnętrznej warstwy górnej

Założono, że należy umożliwić dostęp do wszystkich części użytkowych płytki FOI ustawionej na podporach. Z tego tytułu na warstwie górnej umieszczono wszystkie elementy zawierające wtyki pod przewody, złącze sygnałowe i zasilające oraz punkty pomiarowe.

3.4.3. Widok warstwy środkowej 1 – Middle Layer 1

Warstwa środkowa 1 została przewidziana do rozprowadzenia sygnału masy cyfrowej oraz sygnałów analogowych (Rysunek 21).

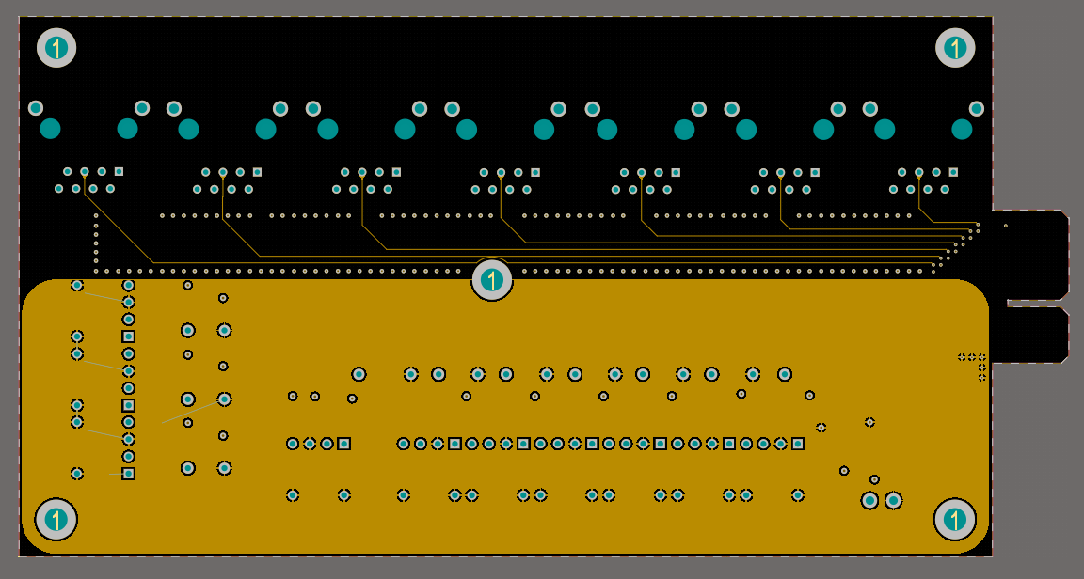
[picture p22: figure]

Rysunek 21. Widok warstwy środkowej 1

Masę cyfrową i masę analogową podłączono do odpowiednich wyprowadzeń na złączu krawędziowym.

3.4.4. Widok warstwy środkowej 2 – Middle Layer 2

Na warstwie środkowej 2 zaplanowano rozprowadzenie sygnałów zasilających (Rysunek 22).

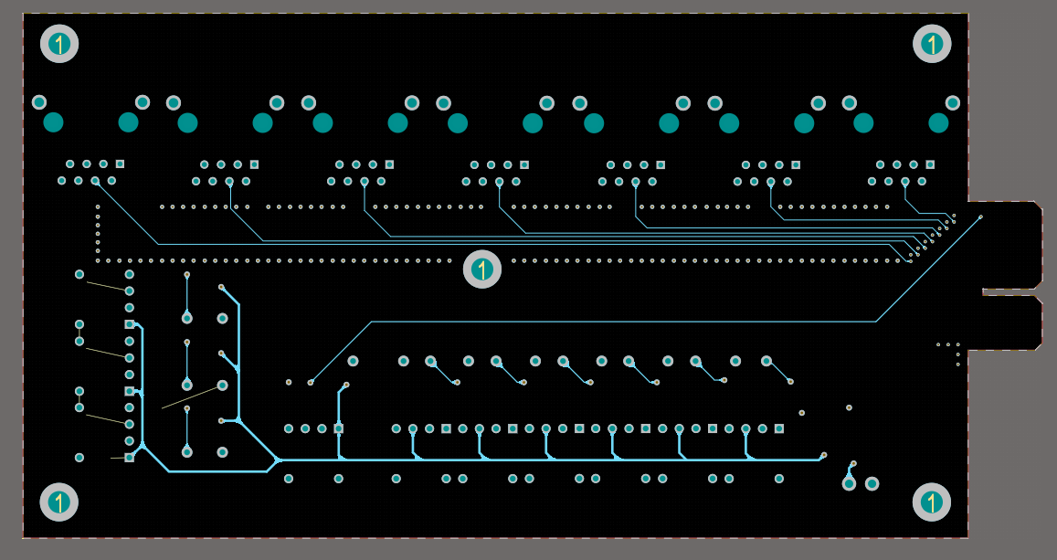
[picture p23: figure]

Rysunek 22. Widok warstwy środkowej 2

Ścieżki poprowadzone na tej warstwie służyły do zasilenia obwodu napięciem 3.3 [V]. Sygnały

poprowadzono zarówno ze złącza krawędziowego jak i z dodatkowego złącza zasilającego.
Przez fizyczną budowę ekranu separującego oraz fakt, że na warstwach sygnałowych znajdowały się jego okładki, na drugiej warstwie środkowej poprowadzono również sygnały analogowe.
3.4.5. Widok zewnętrznej warstwy dolnej – Bottom Layer

Ostatnią warstwą obwodu drukowanego była zewnętrzna warstwa dolna, której wizualizację dwuwymiarową przedstawiono na rysunku 23.

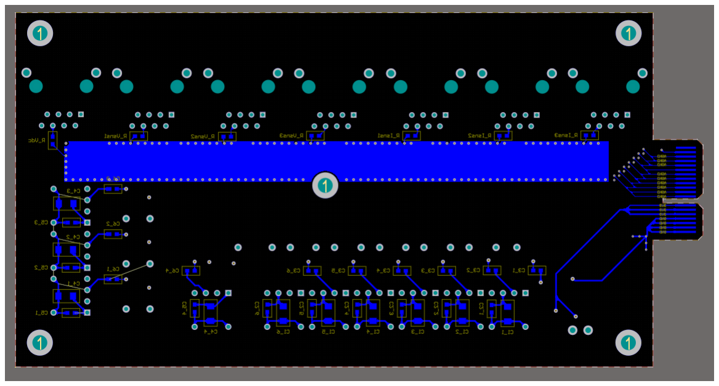
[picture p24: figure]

Rysunek 23. Widok zewnętrznej warstwy dolnej

Sposób połączenia EPC9167 oraz FOI przez nałożenie ich na siebie zakładał wyprowadzenia złącza krawędziowego na dwóch warstwach zewnętrznych więc głównym przeznaczeniem warstwy dolnej było rozprowadzenie części sygnałów pochodzących ze złącza J60.

Ze względu umieszczenia konwerterów światłowodowych na warstwie górnej, ułożono kondensatory stabilizujące napięcie i filtrujące dokładnie pod nimi oraz możliwie najbliżej ich pinów w celu maksymalnego skrócenia ścieżek prądowych.

3.4.6. Wizualizacja 3D

Widoki trójwymiarowe służą do propozycji wyglądu płytki z poziomu projektowego oraz mogą stanowić wzór wykorzystany do procesu montażu. Umieszczono na niej trójwymiarowe wersje komponentów dokładniej opisanych w rozdziale projektowym. Wizualizację trójwymiarową zaprezentowano na rysunku 24 oraz 25.

Rysunek 24. Wizualizacja 3D - widok z góry

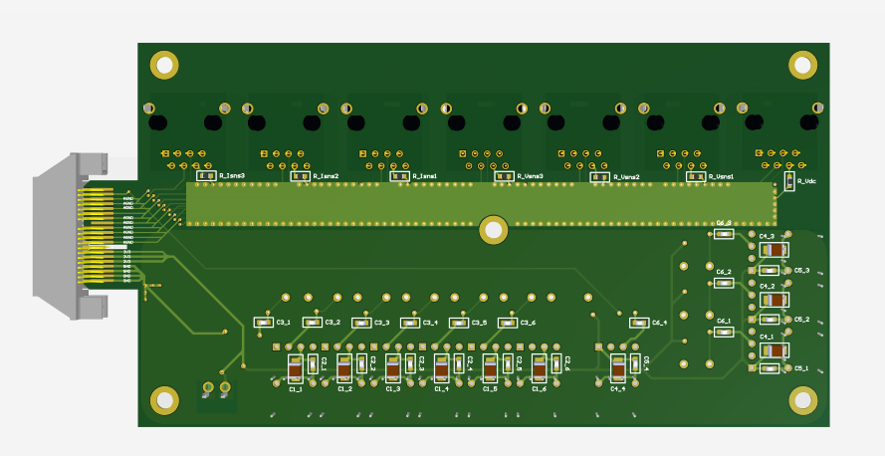
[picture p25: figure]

Rysunek 25. Wizualizacja 3D - widok z dołu

## Rozdział 4 – Montaż elementów elektrycznych oraz wykonanie

## testów poprawności

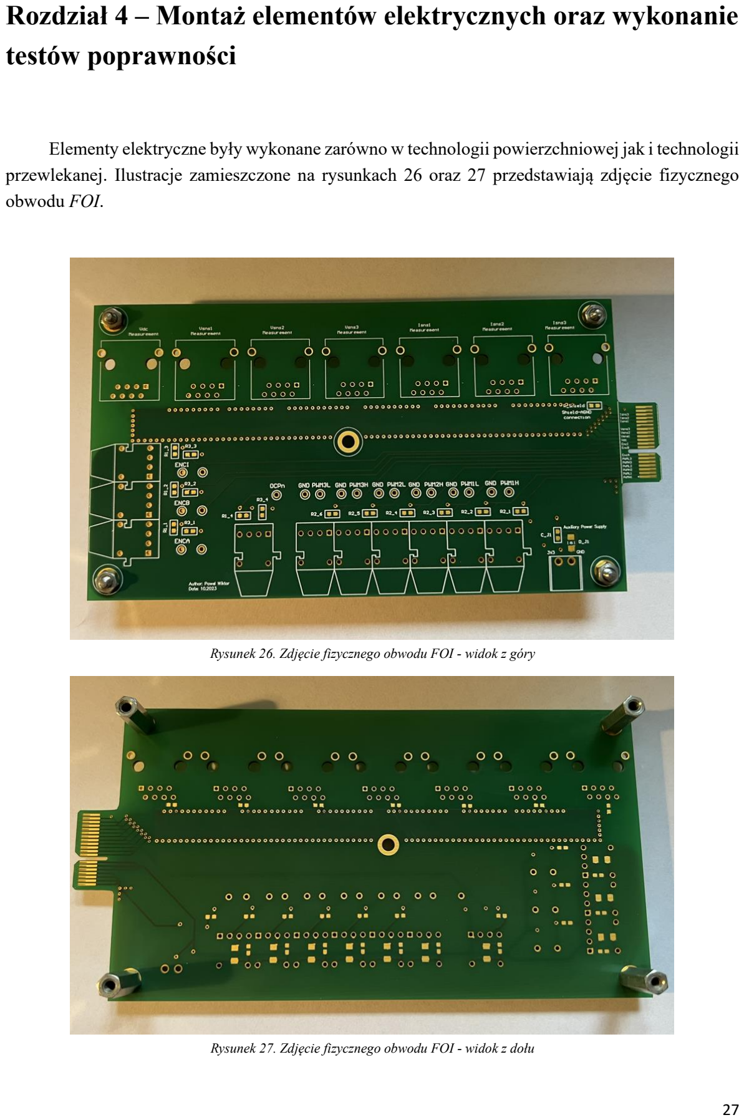
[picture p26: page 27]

Elementy elektryczne były wykonane zarówno w technologii powierzchniowej jak i technologii przewlekanej. Ilustracje zamieszczone na rysunkach 26 oraz 27 przedstawiają zdjęcie fizycznego obwodu FOI.

Rysunek 26. Zdjęcie fizycznego obwodu FOI - widok z góry

Rysunek 27. Zdjęcie fizycznego obwodu FOI - widok z dołu

### 4.1. Testy poprawności

Po otrzymaniu fizycznego obwodu drukowanego od firmy zewnętrznej zajmującej się produkcją należy wykonać szereg czynności pozwalający określić poprawność działania, nazywanych zbiorczo testami poprawności. W przypadku płytek „PCB” za wystarczające kryterium uznaje się weryfikację przewodzenia ścieżek w punktach łączeniowych. Na rysunku 28 zaprezentowano zdjęcie stanowiska pomiarowego do wykonania testów poprawności.


Rysunek 28. Stanowisko do przeprowadzenia testów poprawności

Testy poprawności wykonano wykorzystując multimetr cyfrowy z sondami pomiarowymi w trybie badania ciągłości obwodu.
Sprawdzono ciągłość przewodzenia na liniach sygnałów cyfrowych i analogowych oraz na liniach zasilających.
Zarejestrowano ciągłość na wszystkich badanych ścieżkach co pozwoliło stwierdzić poprawność zaprojektowania i wykonania obwodu oraz przystąpić do etapu montażu.


### 4.2. Lutowanie elementów elektrycznych

Po pomyślnej weryfikacji poprawności obwodu przystąpiono do procesu lutowania. Rozpoczęto od powierzchniowych elementów „0603” od spodniej części płytki, następnie zamontowano elementy wykonane w technologii przewlekanej. Widoki płytki po zakończonym procesie lutowania elementów zestawiono na rysunkach 29 oraz 30.

Rysunek 29. Wygląd końcowy płytki – widok z góry

Rysunek 30. Wygląd końcowy płytki – widok z dołu

## Rozdział 5 – Podsumowanie

Celem projektu dyplomowego było stworzenie obwodu drukowanego, umożliwiającego połączenie obiektu w postaci trójfazowego falownika napięcia EPC9167 dedykowanego do obsługi układów napędowych z silnikami PMSM z systemem szybkiego prototypowania układów sterowania B-BOX firmy „imperix”.
W projekcie dyplomowym opisano stanowisko systemu sterowania, opisano procesy projektowania, montażu i uruchomienia interfejsu oraz spełniono wszystkie założenia i cele projektowe.
W efekcie końcowym interfejs komunikacyjny umożliwia zarówno dwukierunkową konwersję sygnałów elektrycznych w standardzie „TTL” obsługiwanych przez moduł falownika na sygnały w standardzie transmisji światłowodowej obsługiwane przez sterownik B-BOX jak i propagację sygnałów pomiarowych w standardzie analogowym do sterownika wykorzystując złącza RJ-45. Projekt dyplomowy umożliwił mi naukę obsługi profesjonalnego oprogramowania przeznaczonego dla obwodów drukowanych, pogłębienie wiedzy w zagadnieniach sterowania światłowodowego oraz udoskonalenie umiejętności lutowania elementów elektrycznych.

## Bibliografia

[1] Dokumentacja techniczna sterownika imperix B-BOX RCP – “B-BOX_Datasheet”
[2] Dokumentacja techniczno-ruchowa EPC9167 – „EPC9167_qsg”
[3] Krykowski K. – „Silniki PM BLDC”, Wydawnictwo BTC, Legionowo 2015, str. 14-16
[4] „Altium Designer – przewodnik po programie”, Altium Limited, 2005-2019
[5] Strona producenta „SAMTEC”, dedykowana dla urządzenia MEC1-120-02-F-D-EM2 – https://www.samtec.com/products/mec1-120-02-f-d-em2
[6] Dokumentacja techniczna złącza MEC1-120-02-F-D-EM2 – „mec1-1xx-xx-xx-d-emx-xxfootprint”
[7] Strona producenta „BROADCOM”, dedykowana dla urządzenia AFBR-2624Z – https://www.broadcom.com/products/fiber-optic-modules-components/industrial/industrial-controlgeneral-purpose/650nm/afbr-2624z (https://www.broadcom.com/products/fiber-optic-modules-components/industrial/industrial-control-general-purpose/650nm/afbr-2624z)
[8] Strona producenta „BROADCOM”, dedykowana dla urządzenia AFBR-1624Z – https://www.broadcom.com/products/fiber-optic-modules-components/industrial/industrial-controlgeneral-purpose/650nm/afbr-1624z (https://www.broadcom.com/products/fiber-optic-modules-components/industrial/industrial-control-general-purpose/650nm/afbr-1624z)
[9] Strona producenta „Phoenix Contact”, dedykowana dla urządzenia CUC-SP-J1ST-S/R4LT -https://www.phoenixcontact.com/pl-pl/produkty/wkladka-zenska-cuc-sp-j1st-sr4lt-1149872

## Załączniki

[1] Dokumentacja techniczna sterownika „imperix B-BOX RCP” – “B-BOX_Datasheet.pdf”
[2] Dokumentacja techniczno-ruchowa EPC9167 – „EPC9167_qsg.pdf”
[3] Dokumentacja techniczna złącza MEC1-120-02-F-D-EM2 – „mec1-1xx-xx-xx-d-emx-xxfootprint.pdf”

## Spis tabel i rysunków

- Tabela 1. Specyfikacja sterownika „B-BOX RCP” – źródło: dokumentacja techniczna sterownika imperix B-BOX RCP – “B-BOX_Datasheet”
- Tabela 2. Opis indeksowania sygnałów cyfrowych oraz analogowych – opracowanie własne
- Tabela 3. Założenia projektowe – opracowanie własne

________________________________________________________________________________

- Rysunek 1. Schemat blokowy systemu sterowania – źródła:
- Dokumentacja techniczna sterownika imperix B-BOX RCP – “B-BOX_Datasheet”
- Dokumentacja techniczno-ruchowa EPC9167 – „EPC9167_qsg”
- http://kener.elektr.polsl.pl/epedlab/lect.php?no=b5&l=pl
- Rysunek 2. Zdjęcie sterownika imperix B-BOX RCP – źródło: dokumentacja techniczna sterownika imperix B-BOX RCP – “B-BOX_Datasheet”
- Rysunek 3. Koncepcja przyłączenia sygnałów do pinów złącza RJ-45 – źródło: dokumentacja techniczna sterownika imperix B-BOX RCP – “B-BOX_Datasheet”
- Rysunek 4. Schemat elektryczny modułu trójfazowego falownika napięcia – źródło: dokumentacja techniczno-ruchowa EPC9167 – „EPC9167_qsg”
- Rysunek 5. Zdjęcie modułu trójfazowego falownika napięcia– źródło: dokumentacja techniczno-ruchowa EPC9167 – „EPC9167_qsg”
- Rysunek 6. Schemat ideowy systemu sterowania – opracowanie własne
- Rysunek 7. Koncepcja rozmieszczenia elementów na płytce FOI – opracowanie własne
- Rysunek 8. Schemat główny – opracowanie własne
- Rysunek 9. Schemat elektryczny sekcji złącza sygnałowego – opracowanie własne
- Rysunek 10. Zdjęcie złącza krawędziowego, model MEC1-120-02-F-D-EM2 – źródło: https://www.samtec.com/products/mec1-120-02-f-d-em2
- Rysunek 11. Fragment dokumentacji technicznej złącza MEC1-120-02-F-D-EM2 – źródło: Dokumentacja techniczna złącza MEC1-120-02-F-D-EM2 – „mec1-1xx-xx-xx-d-emx-xxfootprint”
- Rysunek 12. Schemat elektryczny sekcji wejść/wyjść cyfrowych – opracowanie własne
- Rysunek 13. Odbiornik światłowodowy, model "AFBR-2624Z" – źródło: https://www.broadcom.com/products/fiber-optic-modules-components/industrial/industrial-control-general-purpose/650nm/afbr-2624z (https://www.broadcom.com/products/fiber-optic-modules-components/industrial/industrial-control-general-purpose/650nm/afbr-2624z)
- Rysunek 14. Schemat elektryczny odbiornika światłowodowego – opracowanie własne
- Rysunek 15. Nadajnik światłowodowy, model „AFBR-1624Z" – źródło: https://www.broadcom.com/products/fiber-optic-modules-components/industrial/industrial-control-general-purpose/650nm/afbr-1624z (https://www.broadcom.com/products/fiber-optic-modules-components/industrial/industrial-control-general-purpose/650nm/afbr-1624z)
- Rysunek 16. Schemat elektryczny nadajnika światłowodowego – opracowanie własne

- Rysunek 17. Schemat elektryczny sekcji wyjść analogowych – opracowanie własne
- Rysunek 18. Zdjęcie złącza typu „RJ-45”, model CUC-SP-J1ST-S/R4LT – źródło: https://www.phoenixcontact.com/pl-pl/produkty/wkladka-zenska-cuc-sp-j1st-sr4lt-1149872
- Rysunek 19. Widok ogólny płytki „FOI” – opracowanie własne
- Rysunek 20. Widok zewnętrznej warstwy górnej – opracowanie własne
- Rysunek 21. Widok warstwy środkowej 1 – opracowanie własne
- Rysunek 21. Widok warstwy środkowej 2 – opracowanie własne
- Rysunek 23. Widok zewnętrznej warstwy dolnej – opracowanie własne
- Rysunek 24. Wizualizacja 3D - widok z góry – opracowanie własne
- Rysunek 25. Wizualizacja 3D - widok z dołu – opracowanie własne
- Rysunek 26. Zdjęcie fizycznego obwodu FOI - widok z góry – opracowanie własne
- Rysunek 27. Zdjęcie fizycznego obwodu FOI - widok z dołu – opracowanie własne
- Rysunek 28. Stanowisko do przeprowadzenia testów poprawności – opracowanie własne
- Rysunek 29. Wygląd końcowy płytki – widok z góry – opracowanie własne
- Rysunek 30. Wygląd końcowy płytki – widok z dołu – opracowanie własne

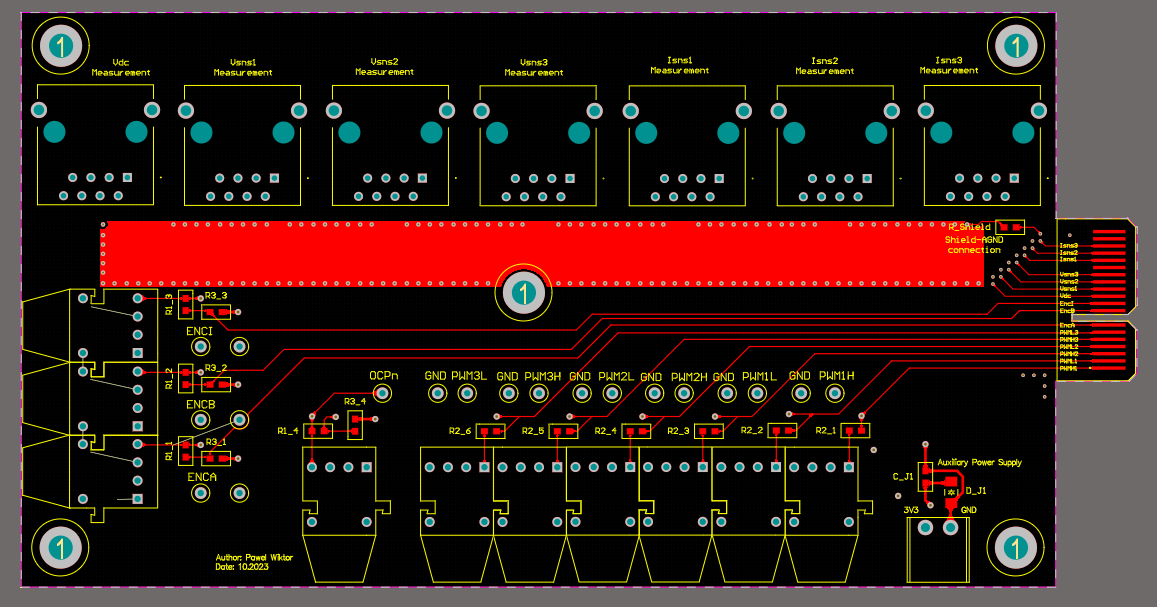
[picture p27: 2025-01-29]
screenshots/Fibre-Optic-Interface_Top_Layer_layout.png

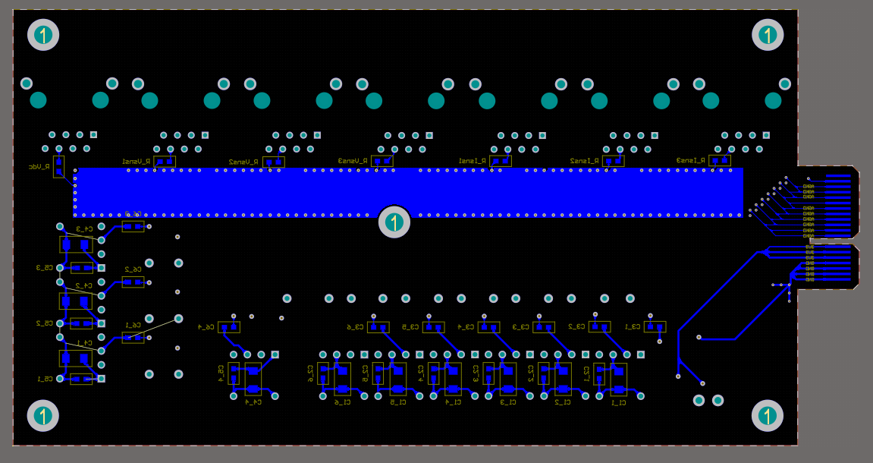
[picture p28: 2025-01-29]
screenshots/Fibre-Optic-Interface_Bottom_Layer_layout.png

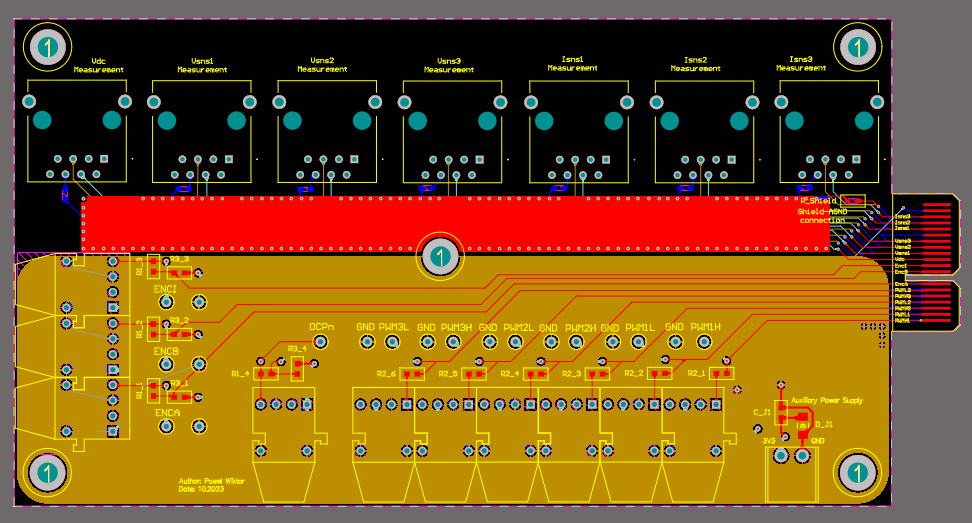
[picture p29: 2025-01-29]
screenshots/Fibre-Optic-Interface_overall_layout.png

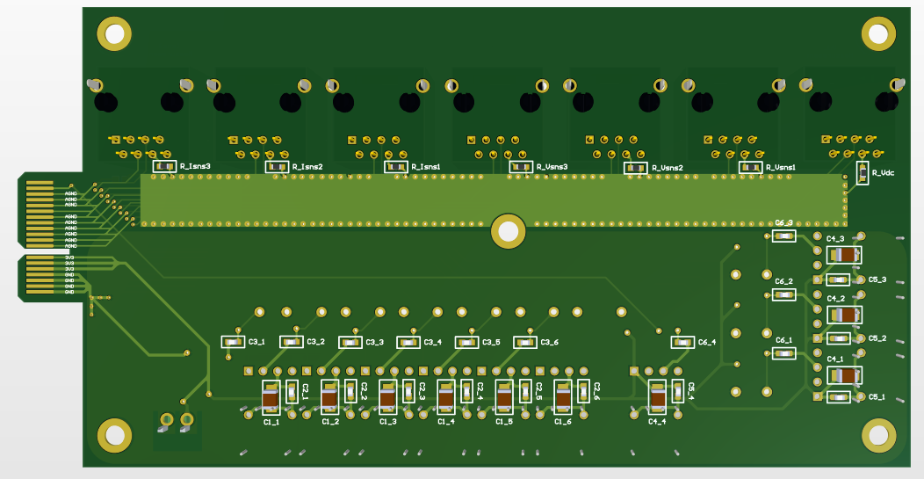
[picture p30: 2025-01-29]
screenshots/3d-Bottom_View.png

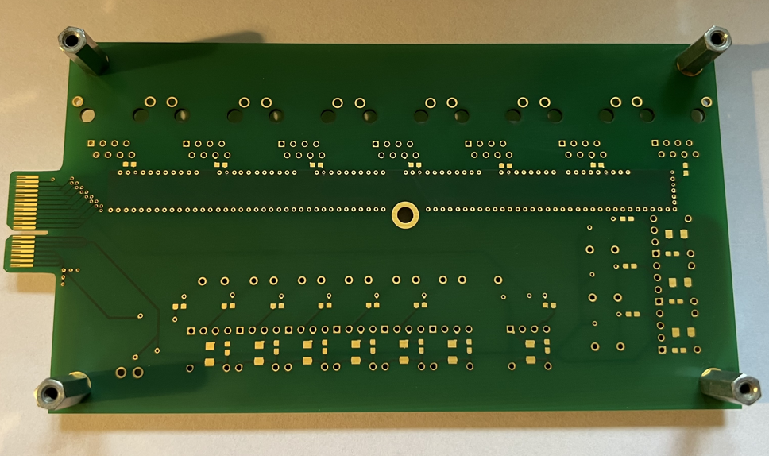
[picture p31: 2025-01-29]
screenshots/pcb_back_view_after_etching.png

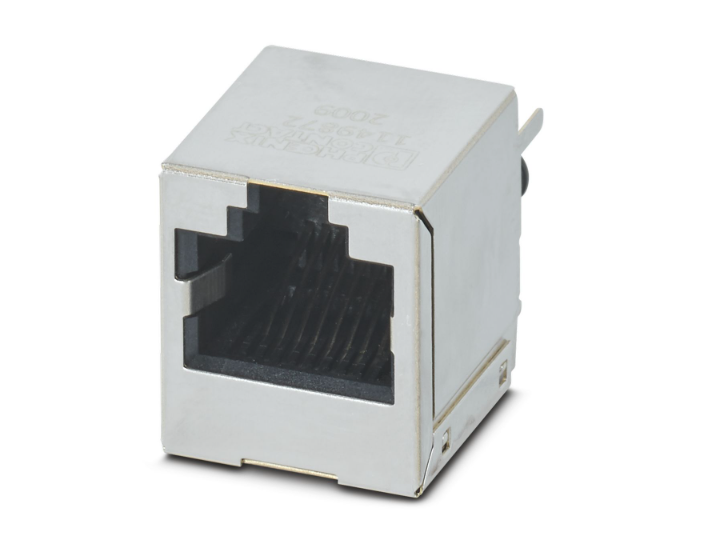
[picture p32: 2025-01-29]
screenshots/CUC-SP-J1ST-S R4LT.png

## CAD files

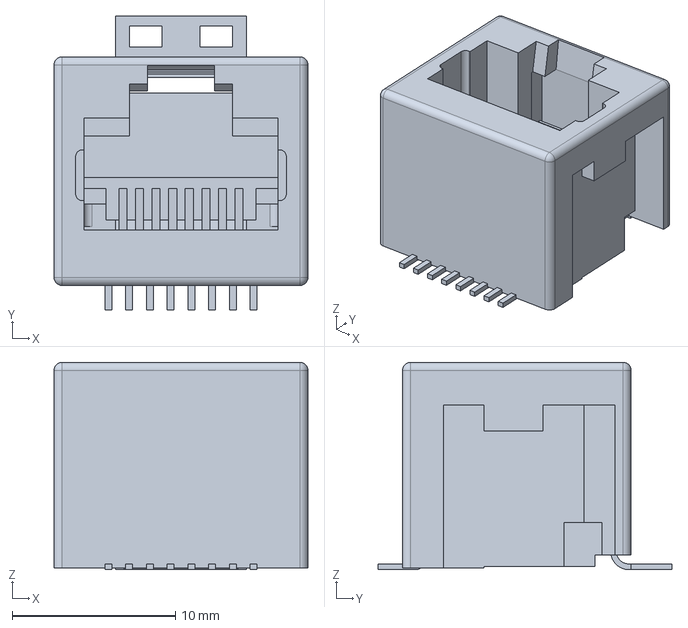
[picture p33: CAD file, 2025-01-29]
main/3D models/4_338088_3/c-4-338088-3-y-3d.stp
15.6 x 18.0 x 12.7 mm

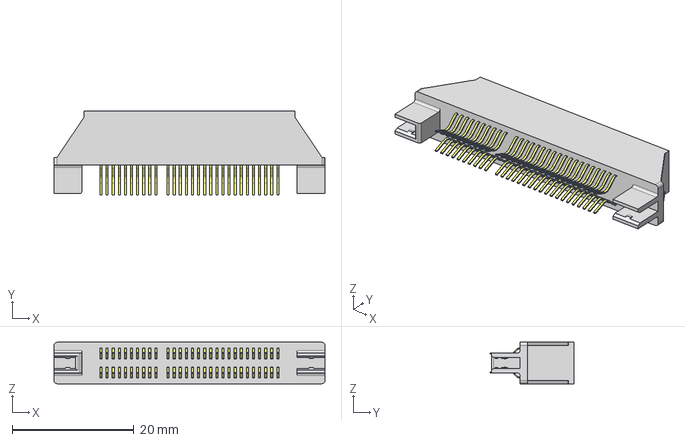
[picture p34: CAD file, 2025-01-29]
main/3D models/PARTserver22023111520412969424711d0b6156e/MEC1-130-02-F-D-EM2-TR.stp
44.4 x 13.8 x 6.81 mm
MEC1-130-02-D-EM2_pins
MEC1-130-02-D-EM2_socket

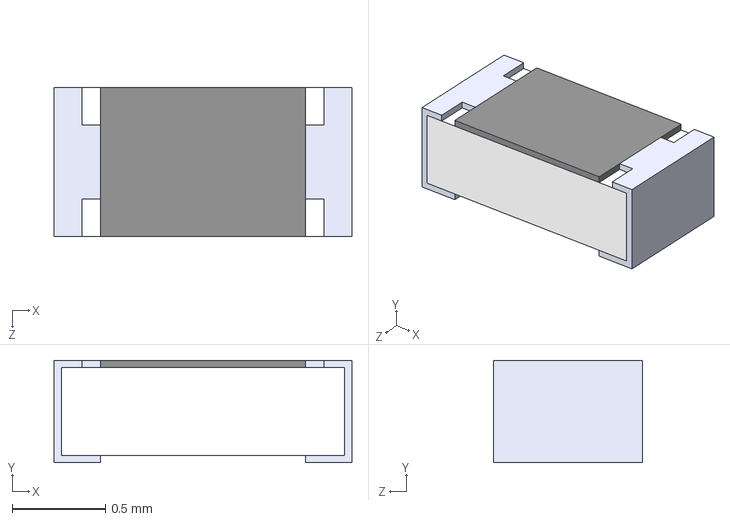
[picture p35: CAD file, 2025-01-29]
main/3D models/RC0603FR_074K7L/RC0603FR-074K7L.step
1.60 x 0.55 x 0.8 mm

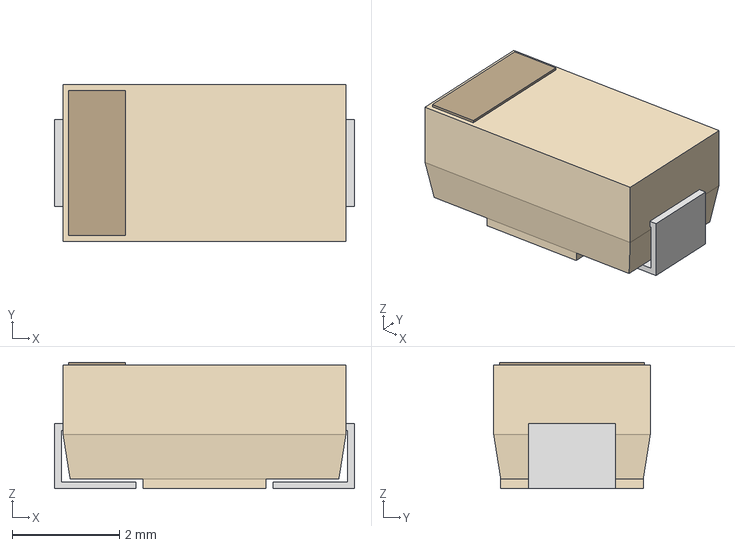
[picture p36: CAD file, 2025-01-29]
main/3D models/SMAZ15_13_F/AltiumDesigner/SMA_DIO.step
5.59 x 2.92 x 2.35 mm

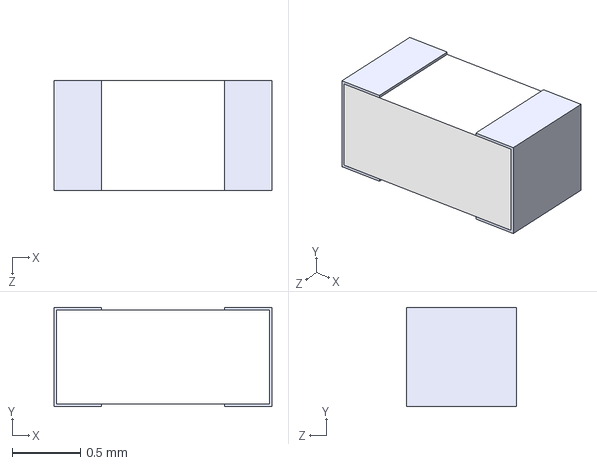
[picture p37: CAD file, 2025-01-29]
main/3D models/06035J100JBTTR.STEP
1.60 x 0.73 x 0.81 mm

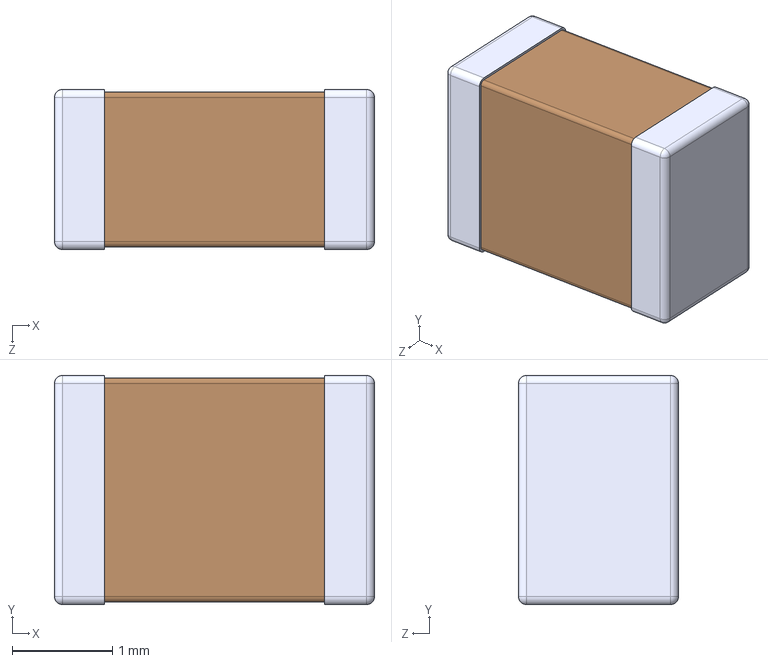
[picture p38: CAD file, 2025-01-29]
main/3D models/12063C106KAT2A/12063C106KAT2A.step
3.20 x 2.29 x 1.60 mm

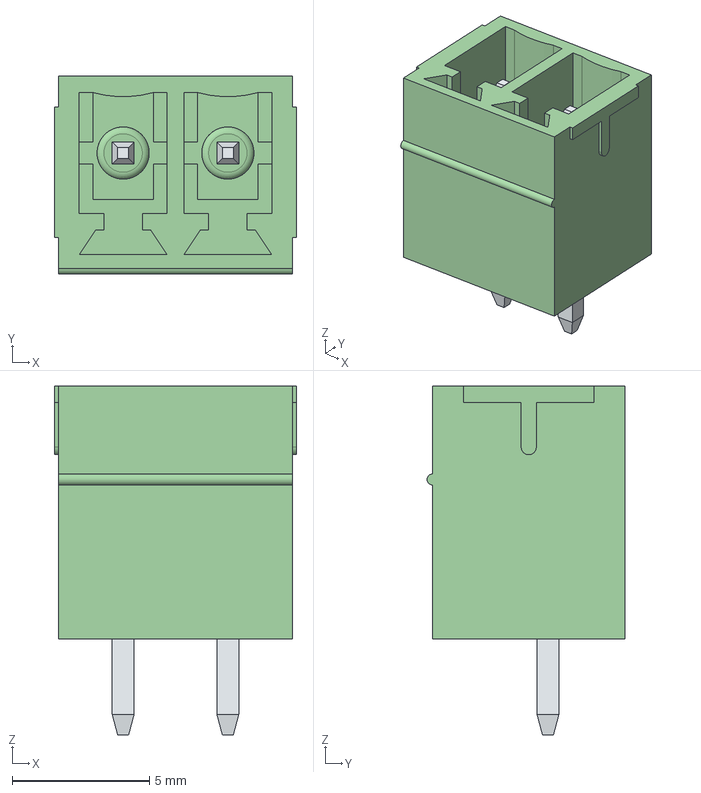
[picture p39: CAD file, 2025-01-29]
main/3D models/691321300002 (rev1).stp
8.81 x 7.20 x 12.7 mm
6913213000xx_PIN x 2

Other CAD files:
schematics/layout_concept.dwg
schematics/block_diagram_detailed.dwg

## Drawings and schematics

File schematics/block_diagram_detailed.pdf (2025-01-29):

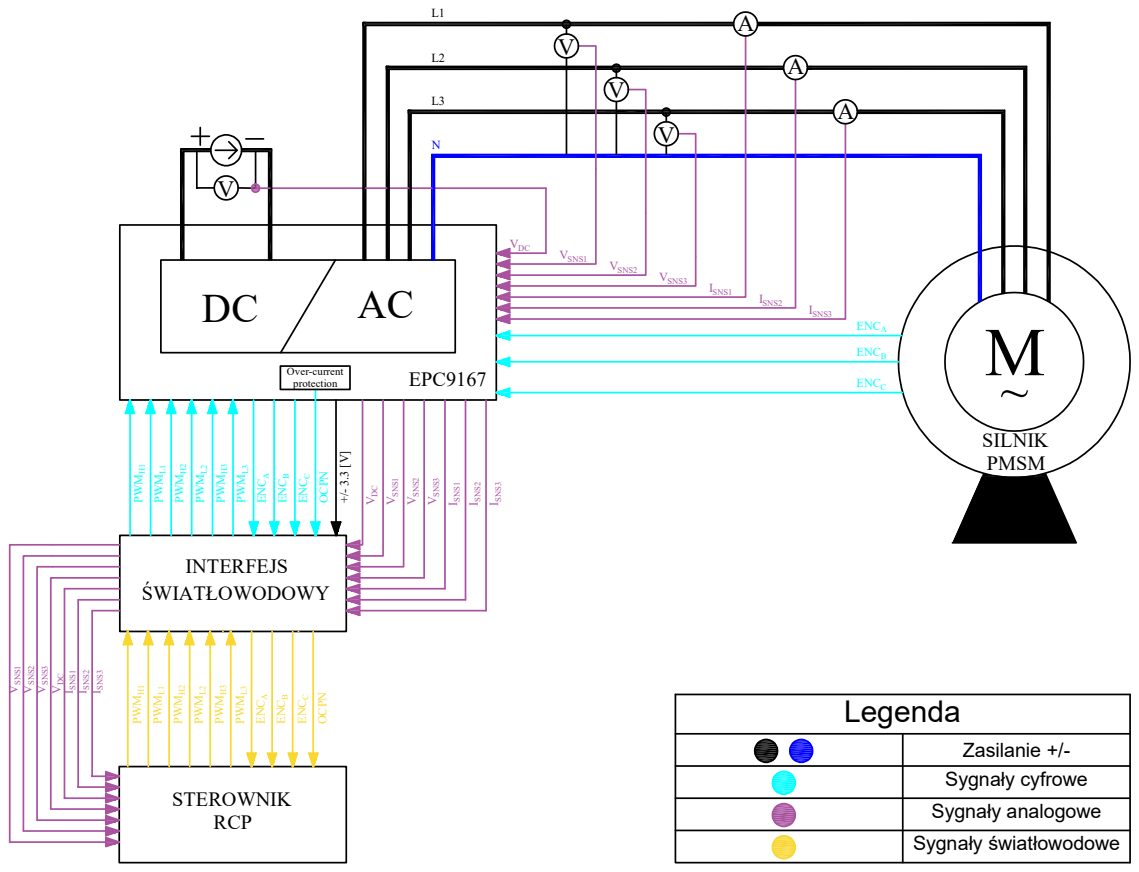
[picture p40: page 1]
INTERFEJS ŚWIATŁOWODOWY; SILNIK PMSM; STEROWNIK; RCP PWMH¹; PWML¹; PWMH²; PWML²; PWMH³; PWML³; ENCA; ENCB; ENCC; OCPN PWMH¹; OCPNVSNS¹ VSNS² VSNS³ VDC; ISNS1 ISNS2 ISNS3 VDC VSNS1 VSNS2 VSNS3; ISNS1 ISNS2 ISNS3; Legenda; Zasilanie +/- Sygnały cyfrowe; Sygnały analogowe; Sygnały światłowodowe ⁺/- 3.3 [V]; M~ EPC9167; VDC; VSNS1; VSNS2; VSNS3; ISNS1; ISNS2; ISNS3; Over-current protection

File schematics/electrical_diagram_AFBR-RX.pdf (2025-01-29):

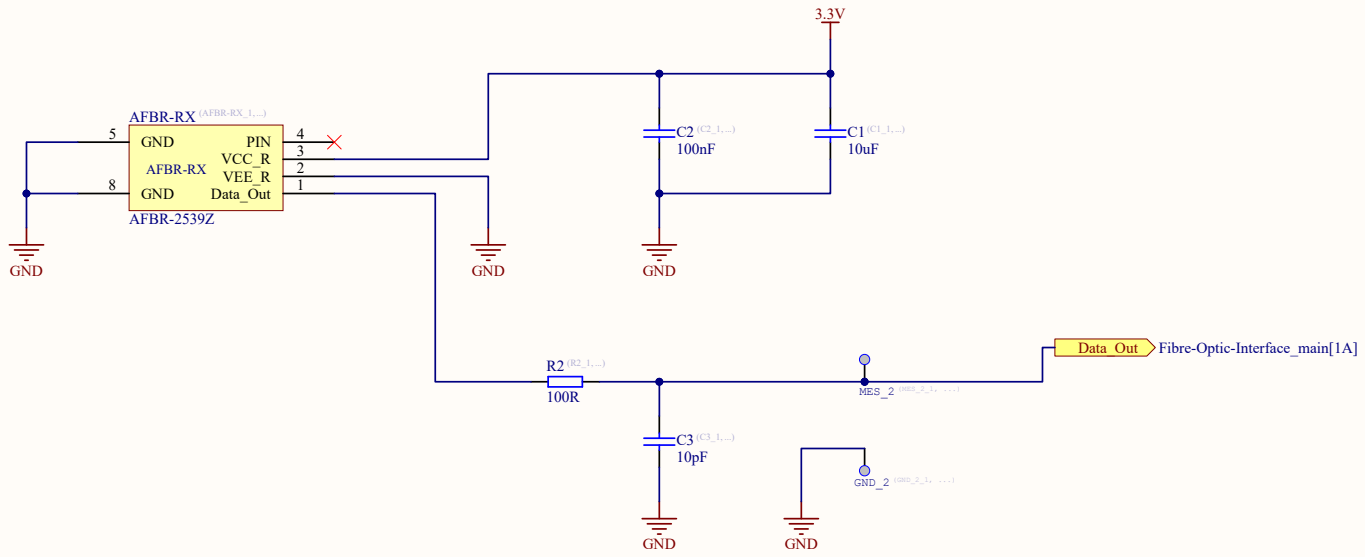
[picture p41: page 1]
GND 8; Data_Out; VEE_R; VCC_R; PIN; AFBR-RX; AFBR-2539Z; GND; Fibre-Optic-Interface_main[1A]; MES_2 ⁽MES_2_1, ...); GND_2 ⁽GND_2_1, ...)

AFBR-RX ⁽AFBR-RX_1, ...)
GND 5

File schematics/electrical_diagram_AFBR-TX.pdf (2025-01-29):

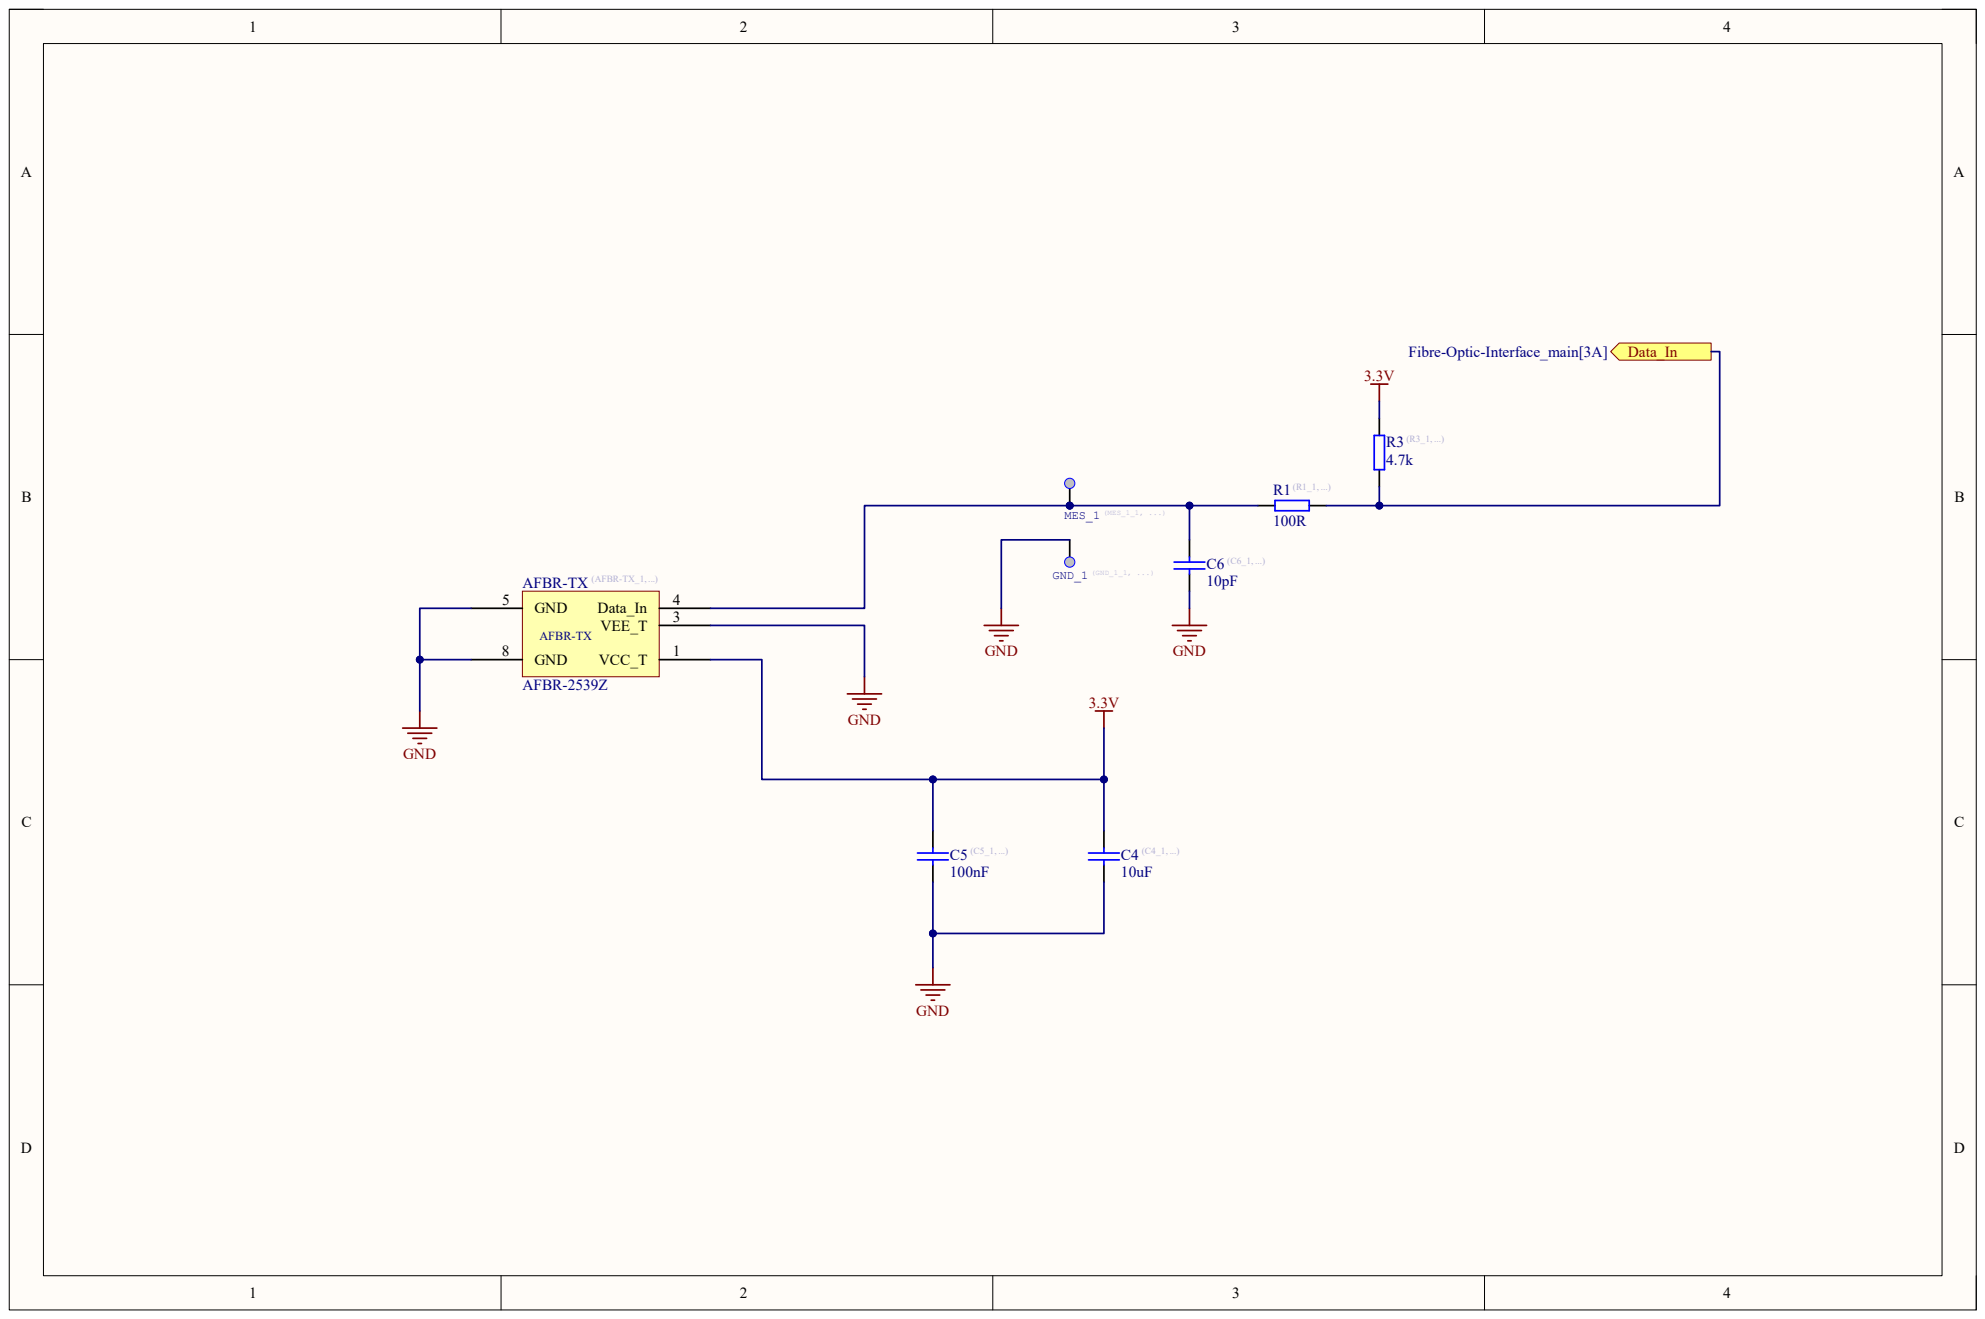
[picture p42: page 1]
GND 8; Data_In; VEE_T; VCC_T; AFBR-TX; AFBR-2539Z; GND; Fibre-Optic-Interface_main[3A] Data_In; GND_1 ⁽GND_1_1, ...); 100R MES_1 ⁽MES_1_1, ...)

AFBR-TX ⁽AFBR-TX_1, ...)
GND 5

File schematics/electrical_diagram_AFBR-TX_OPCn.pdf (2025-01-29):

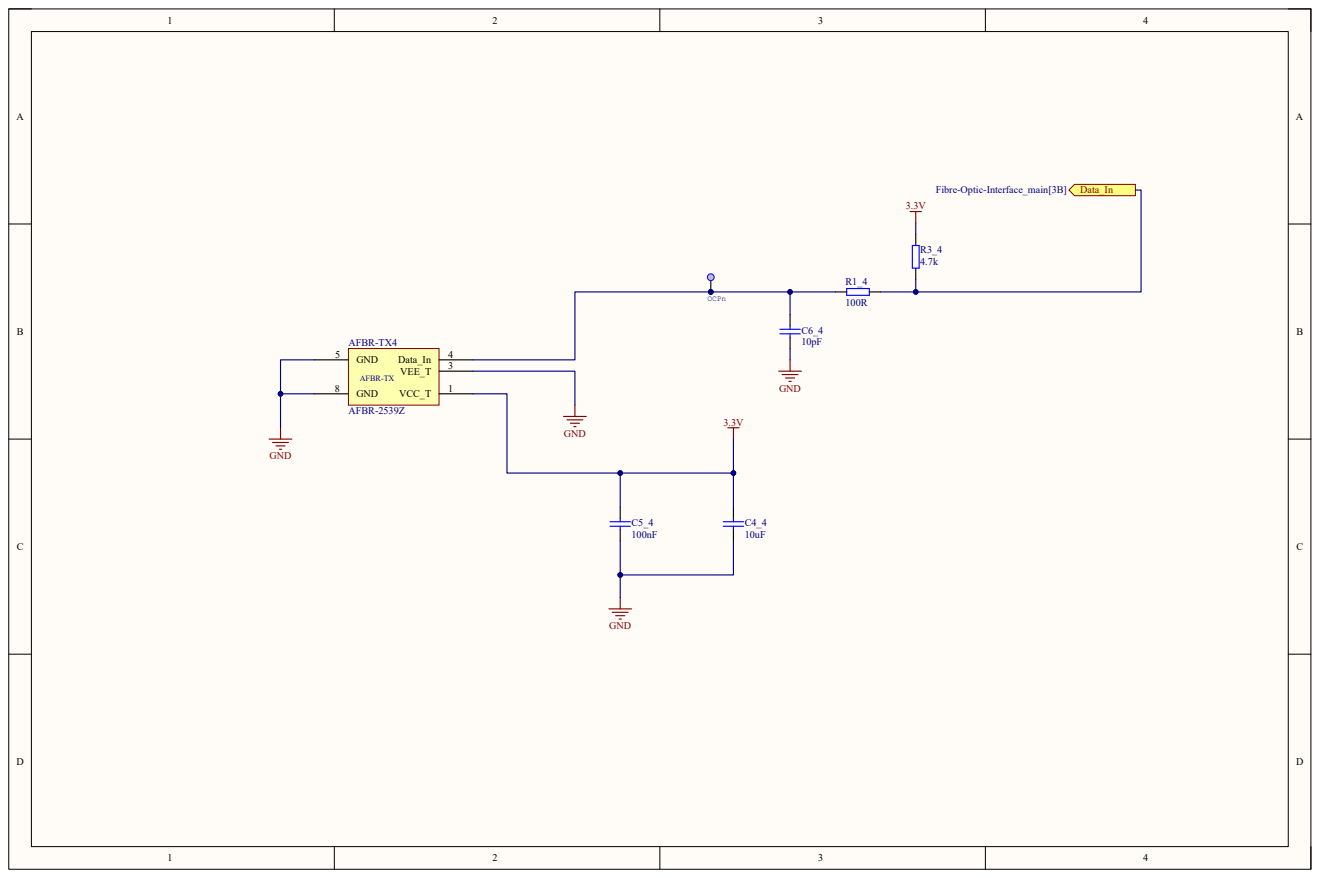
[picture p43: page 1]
GND 5; GND 8; Data_In; VEE_T; VCC_T; AFBR-TX; AFBR-TX4; AFBR-2539Z; GND; Fibre-Optic-Interface_main[3B] Data_In; 100R OCPn

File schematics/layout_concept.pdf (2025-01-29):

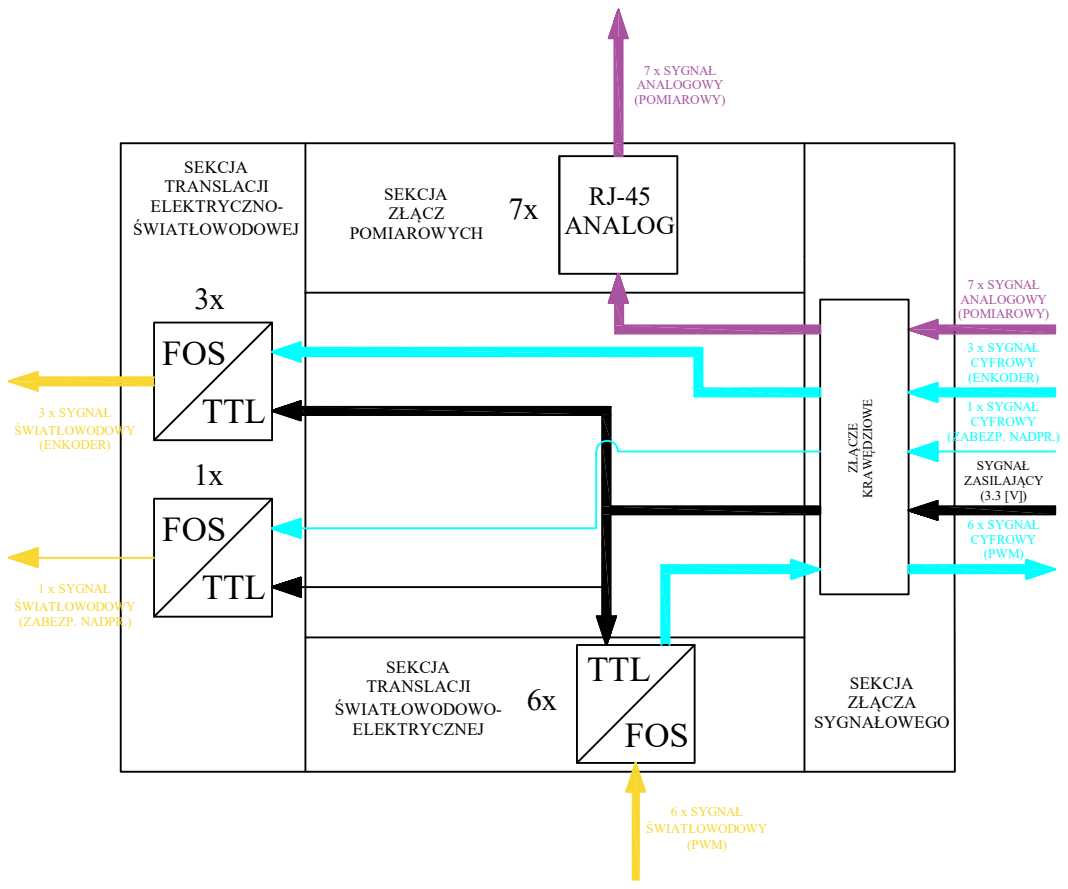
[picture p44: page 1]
SEKCJA ZŁĄCZ POMIAROWYCH; SEKCJA TRANSLACJI ELEKTRYCZNO- ŚWIATŁOWODOWEJ; SEKCJA ZŁĄCZA; SYGNAŁOWEGO ZŁĄCZE KRAWĘDZIOWE; SEKCJA TRANSLACJI ŚWIATŁOWODOWO- ELEKTRYCZNEJ; TTL; FOS; RJ-45 ANALOG; 3 x SYGNAŁ CYFROWY (ENKODER); 7 x SYGNAŁ ANALOGOWY (POMIAROWY); 1 x SYGNAŁ CYFROWY (ZABEZP. NADPR.); SYGNAŁ ZASILAJĄCY (3.3 [V]); 6 x SYGNAŁ CYFROWY (PWM); 6 x SYGNAŁ ŚWIATŁOWODOWY (PWM); 1 x SYGNAŁ ŚWIATŁOWODOWY (ZABEZP. NADPR.); 3 x SYGNAŁ ŚWIATŁOWODOWY (ENKODER)

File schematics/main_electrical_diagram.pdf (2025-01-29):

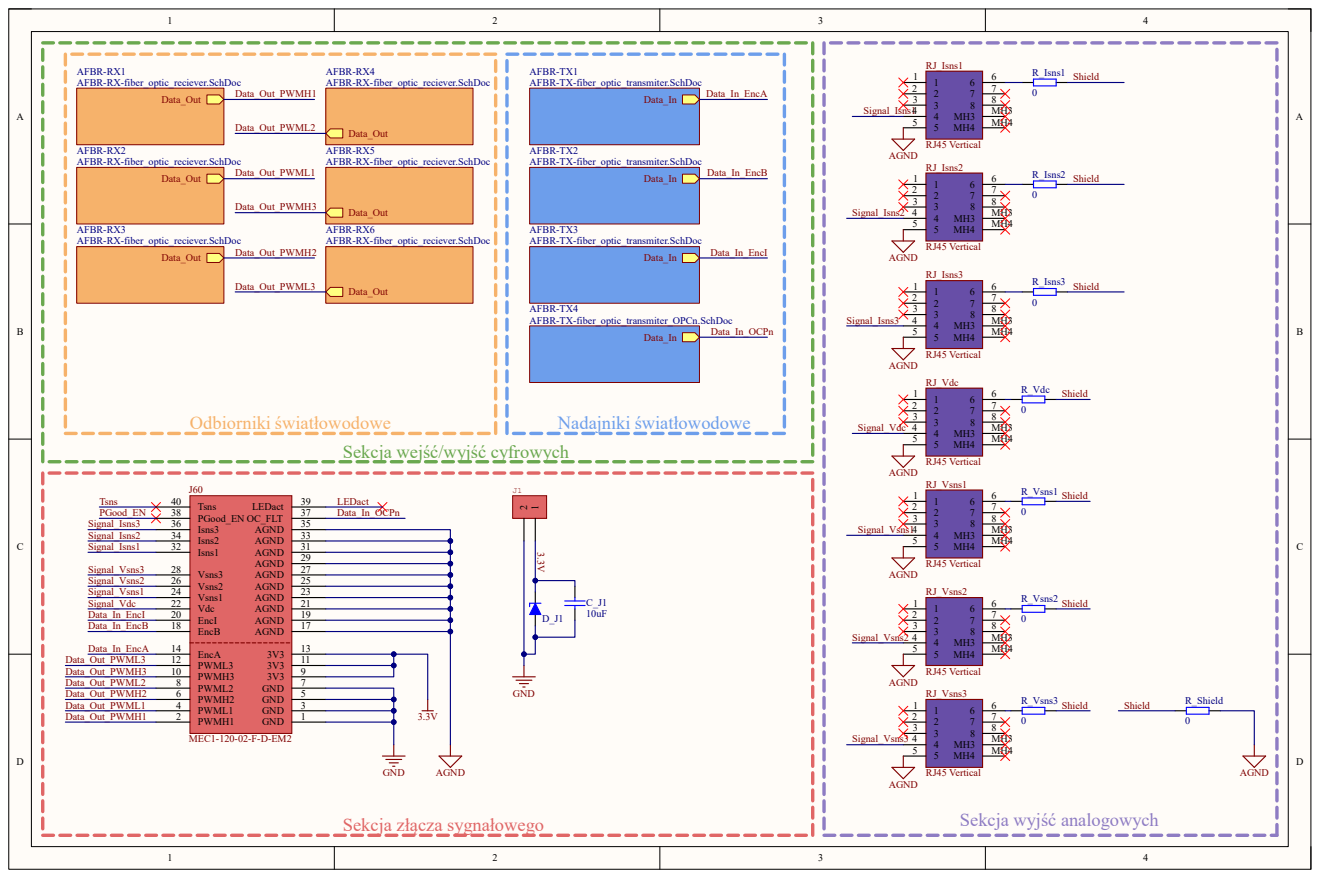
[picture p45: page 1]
Data_Out; Data_In; AFBR-RX5 AFBR-RX-fiber_optic_reciever.SchDoc; AFBR-RX6 AFBR-RX-fiber_optic_reciever.SchDoc; Odbiorniki światłowodowe; Nadajniki światłowodowe; Tsns PGood_EN Signal_Isns3 Signal_Isns2 Signal_Isns1; Signal_Vsns3 Signal_Vsns2 Signal_Vsns1 Signal_Vdc Data_In_EncI Data_In_EncB; Data_In_EncA Data_Out_PWML3 Data_Out_PWMH3; Data_Out_PWMH1; Data_Out_PWML1; Data_Out_PWMH2; Data_Out_PWML2; Data_Out_PWMH3; Data_Out_PWML3; Data_In_EncA; Data_In_EncB; Data_In_EncI; GND; AGND; PWMH1 2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

AFBR-RX1
AFBR-RX-fiber_optic_reciever.SchDoc

AFBR-RX4

AFBR-TX1
AFBR-TX-fiber_optic_transmiter.SchDoc

AFBR-RX2

AFBR-TX2

AFBR-RX3

AFBR-TX3

AFBR-TX4
AFBR-TX-fiber_optic_transmiter_OPCn.SchDoc

Sekcja wejść/wyjść cyfrowych

Sekcja złącza sygnałowego

Sekcja wyjść analogowych

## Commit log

2025-01-29 adding schematics
    [block_diagram_detailed.dwg, layout_concept.dwg]
2025-01-29 adding main AD files
    [06035J100JBTTR.STEP, 12063C106KAT2A.step, 691321300002 (rev1).stp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]

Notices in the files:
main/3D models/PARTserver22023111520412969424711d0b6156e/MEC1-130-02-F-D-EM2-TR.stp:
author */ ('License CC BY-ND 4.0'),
